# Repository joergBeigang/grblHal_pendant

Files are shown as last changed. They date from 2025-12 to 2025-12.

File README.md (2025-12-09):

# grblHal_pendant
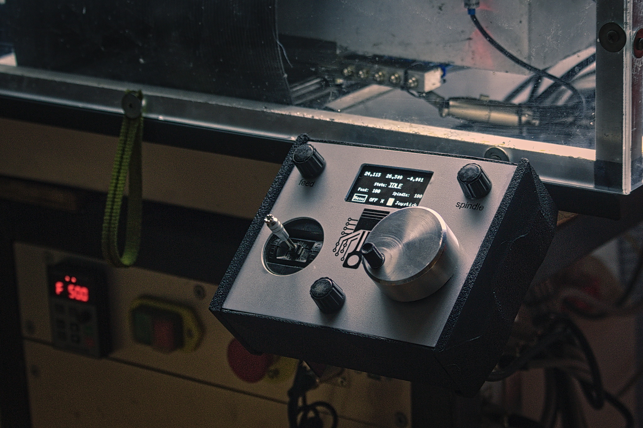
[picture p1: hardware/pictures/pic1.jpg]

This is a simple pendant for [grblHal](https://github.com/grblHAL/core) controlled cnc machines. It is running on an ESP32. For the analog feel it is using a high resolution rotary encoder (with 600 pulses per revolution), and an analog joystick for rapid movement.

There are in total 3 EC11 rotary encoders with button functionality. Two to dial in the feed and spindle overrides, and one for navigating the menu. The display is a I2C OLED (SSD1309) with 128x64 pixel resolution.

I chose those components mostly because I already had them laying around — the rotary encoder came out of an old pendant I made for 8bit grbl back then, the joystick out of an old RC controller. EC11s and the OLED display can be ordered very cheaply from China.

I am aware that my choice for the encoder for jogging is a little bit unconventional, and therefore building a pendant like this is not for everyone, but at least some code snippets might be useful for others.

All the jogging, regardless if joystick or encoder, is done by reading the input device at a frequency of 10Hz. I figured that is a good frequency to feed jogging commands to grbl or grblHal. The revolution of the rotary encoder is translated directly into the revolution of my ball screw, so one revolution moves the machine by 5mm. 1200 edges per revolution means that one pulse equals 0.0042mm movement. With the given time interval of 0.1 seconds the feed is easy to calculate and it has the nice side effect that there is no need for any stop-jog real-time commands. This gives a pretty secure feeling when jogging.

I personally often like to touch off with a running spindle, when preparing stock with an indexed end mill for example. And like this, this feels really smooth.

The UART mode of grblHal is enabled and disabled automatically. So you can switch between the computer and pendant without pressing any buttons. GrblHal needs to be configured with UART mode enabled and rt command for switching over.

---

## Building

The code uses the Arduino framework and a few libraries:

- **U8g2lib.h** and **Wire.h** – for the display  
- **Button.h** and **AiEsp32RotaryEncoder.h** – for the buttons of the EC11 encoders  
- **Preferences.h** – for saving settings in the ESP32  
- **queue** – for streaming gcode  
- **math.h**

It can be compiled and uploaded with the Arduino IDE or the Arduino CLI tools.

Pin assignments and the definition of the pulses per revolution of the rotary encoder can be found in `config.h`. The analog joystick needs to be calibrated first; this can be done in the menu of the pendant. This is important — otherwise the machine might move unexpectedly as soon as joystick input is selected.

---

## Hardware

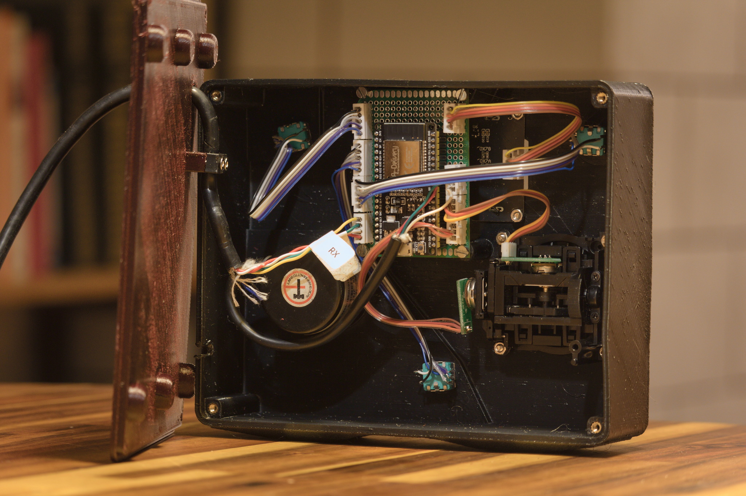
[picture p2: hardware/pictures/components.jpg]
components


In the hardware folder is a schematic and CAD files of the case. I am using 3mm alu dipond as front panel (again, because I found some in my garage). 3mm is a pretty unusual thickness for front panels, so most likely the model needs to be adapted a little, or just 3D-print a spacer that goes under the panel.

And yes, the case is quite big — that's because I'm not a big fan of handheld devices. I prefer it mounted to the CNC so I have one hand free to slide a parallel around on the work piece or similar.

List of components:

- 1 rotary encoder LPD3806-600BM-G5-24G
- 3 rotary encoders EC11
- 1 OLED display 128x64 pixel I2C with SSD1309 driver
- 1 analog joystick
- 1 ESP32 Development board
- 1 bidirectional 2 channel level shifter
- cables and connectors

---

## USE

All the pins, the pulses per revolution of the rotary encoder for jogging and the distance pro revolution are set in config.h.
When it's all connected, and the firmware is flashed the display should show up. 
It needs to be setup in Menu -> Settings:

- Joystick settings
  - Calibrate Joystick - calibration process for the analog joystick 
  - joystick invert X, Y - invert the axis
  - set joystick speed - it is not a real world unit. Standard is 3, 5 gives you about 4200 mm/min feed when jogging full speed in xy direction (diagonal), if Z is moved simultaneous, the feed is higher.

- Encoder settings - invert X, Z and Z
- delay compensation - compensates for delay (processing, acceleration). smaller value give a directer control, less overshoot, higher value smoother movement in higher speeds. Default is 0, values like 0.1 to 0.25 can smoothen joystick jogging

- **Button.h** and **AiEsp32RotaryEncoder.h** – for the buttons of the EC11 encoders  

---

## Disclaimer

Use at your own risk: read the source code first. Don't crash the machine or even hurt yourself.

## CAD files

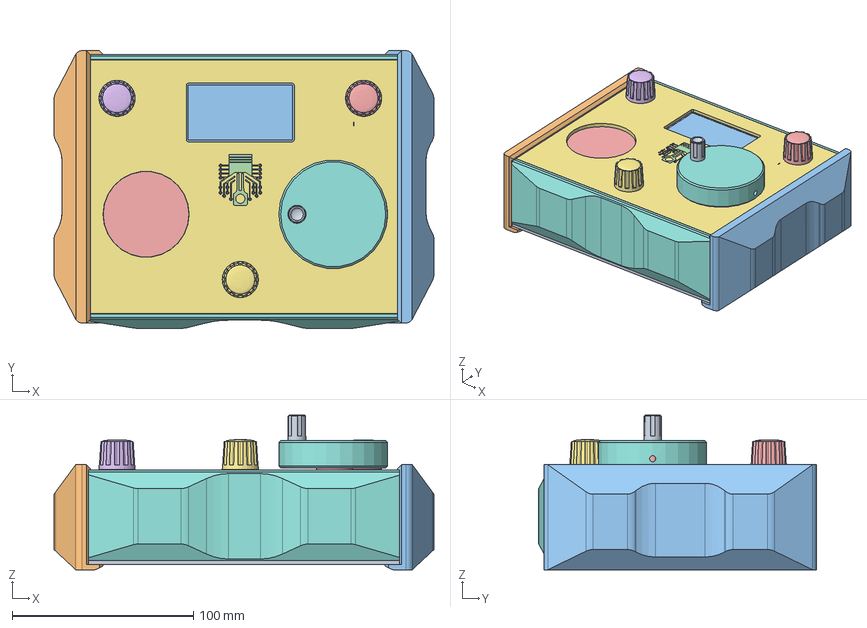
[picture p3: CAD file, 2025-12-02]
hardware/grblHal_pendant_case.FCStd
209.6 x 153.2 x 85.3 mm
ShapeString
ShapeString001
ShapeString002
knob
knob002
knob001
encoder_disk
cable_block
OLED
XH-4P
Joystick
ESP32
a
b
c
d
e
f
rotary_encoder
board
front_panel
case_upper
case_lower
side_cover
side_cover (mirrored)

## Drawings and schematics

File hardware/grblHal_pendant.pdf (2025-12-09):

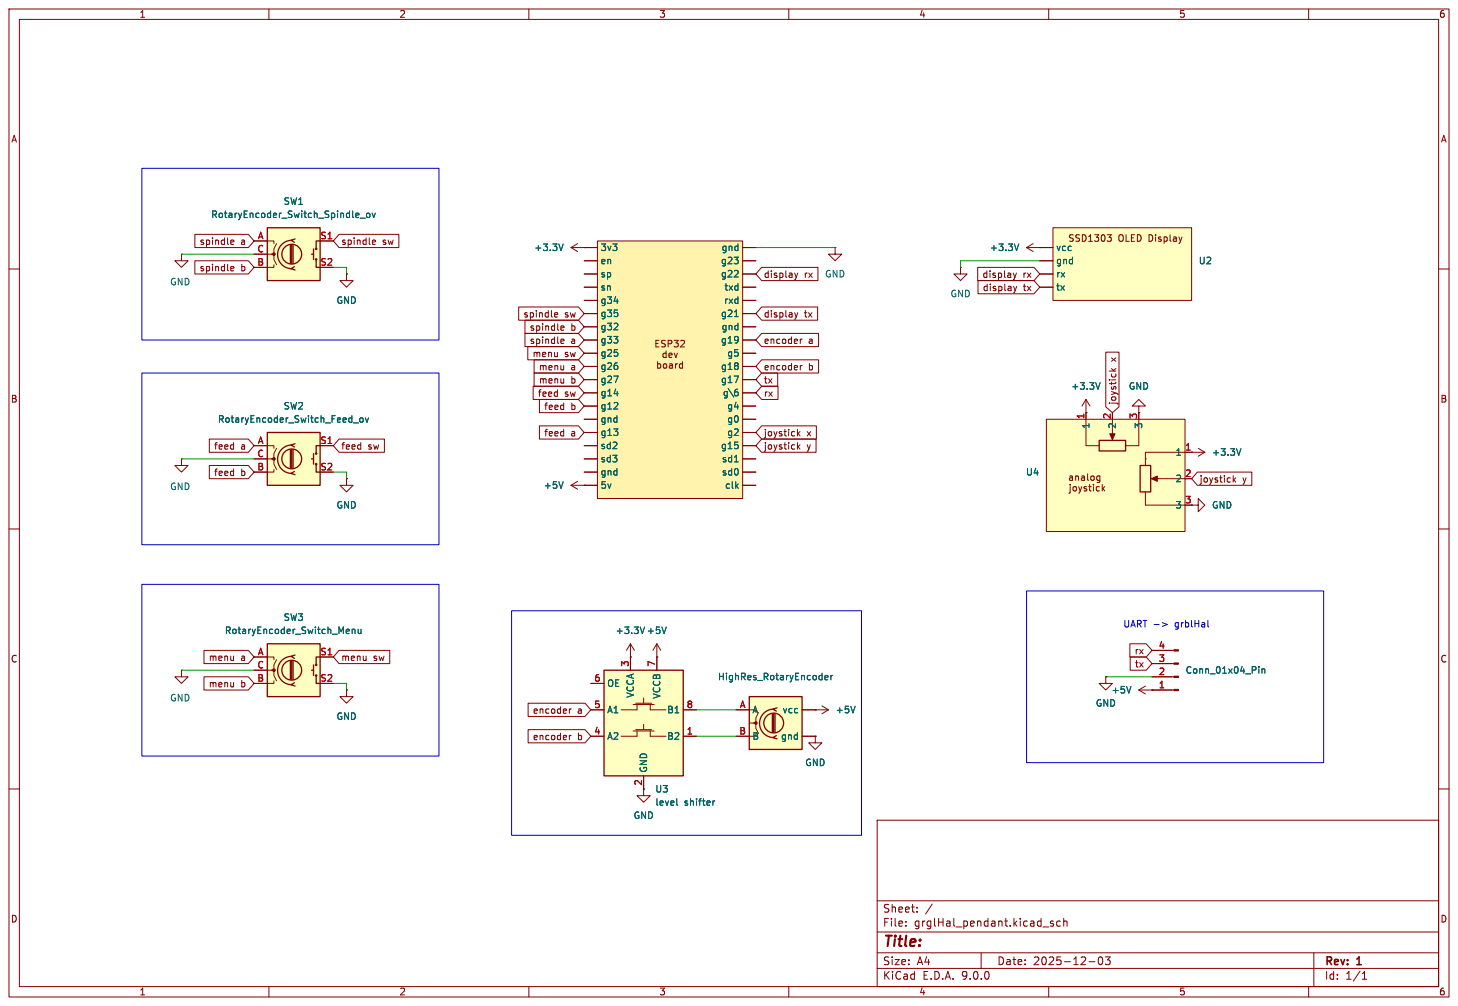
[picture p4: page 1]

Id: 1/1 Title: File: grglHal_pendant.kicad_sch Sheet: /

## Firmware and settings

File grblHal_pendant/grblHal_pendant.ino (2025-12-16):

/*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
grblMachinist is distributed in the hope that it will be useful,
but WITHOUT ANY WARRANTY;
without even the implied warranty of MERCHANTABILITY or FITNESS FOR A PARTICULAR
PURPOSE.
See the GNU General Public License for more details.

You should have received a copy of the GNU General Public License along with
grblMachinist.
If not, see <https://www.gnu.org/licenses/>.
*/

#include <U8g2lib.h>
#include <Wire.h>
#include <math.h>
#include <Button.h>
#include "AiEsp32RotaryEncoder.h"
#include "config.h"
#include "settings.h"
#include "encoder.h"
#include "joystick.h"
#include "parser.h"
#include "gui_render.h"
#include "gui_build.h"
#include "gui_menu_actions.h"
#include <Preferences.h>
#include "ec11_encoder.h"
#include "stream.h"

Preferences prefs;
// instace the settings struct
Settings settings;

// selected menu item
int selectedIndex = -1;          // 1 = off is selected on startup

// to keep UART active while
volatile bool keepActive = false; 

// timer for real time command, used for swtiching on in 
// joystick and encoder reading to avoid too fast switching
// and grblHal freezinguG
long rtCmdTimer = 0;

// timer for swtiching off UART Mode. 
// needs to be reset to keep UART active
// used for jogging with encoder and joyustick
long timerEncoderRest  = 0;

// position of the cursor in the menu
int cursorPosition = 0; 

// mode = operation mode
// 0 - off
// 1 - joystick mode
// 2 - X axis encoder mode
// 3 - Y axis encoder mode
// 5 - machine is in run state
int mode = 0;                   

// the value that is edited in the menu via menu encoder
float valueEdit = 0.0;  

// pointer to valueEdit to use in struct (expects pointer)
float  *pValueEdit = &valueEdit;


// instace of struct that collects all info send by grbl
GrblStatus grblStatus;

// display
U8G2_SSD1309_128X64_NONAME2_F_HW_I2C u8g2(U8G2_R0, U8X8_PIN_NONE);

// E11 rotary encoders
// rotary encoder menu
AiEsp32RotaryEncoder rotaryMenu(MENU_A, MENU_B, -1, -1, 4);
// rotary encoder feed override
AiEsp32RotaryEncoder rotarySpindle(SPINDLE_A, SPINDLE_B, -1, -1, 4);
// rotary encoder spindle override
AiEsp32RotaryEncoder rotaryFeed(FEED_A, FEED_B, -1, -1, 4);

// buttons of rotary encoders, button libraray for easier release detection
Button buttonMenu(MENU_SW);
Button buttonFeed(FEED_SW);
Button buttonSpindle(SPINDLE_SW);

// ISR – reading the EC11 encoders
void IRAM_ATTR readEncoderISR() {
  rotaryMenu.readEncoder_ISR();
  rotaryFeed.readEncoder_ISR();
  rotarySpindle.readEncoder_ISR();
}


// give grblStatus some initial values not avoid pointer errors
void initGrblStatus(){
  grblStatus.status = "NONE";
  grblStatus.position[0] = -331.0;
  grblStatus.position[1] = -912.0;
  grblStatus.position[2] = -183.0;
  grblStatus.overRides[0] = 100.0;
  grblStatus.overRides[1] = 100.0;
  grblStatus.overRides[2] = 100.0;
  grblStatus.coordinateSystem = 54;
}


void setup() {
  // initial values of grblStatus
  initGrblStatus();
  // peferences
  prefs.begin("settings");
  readSettings();
  // Serial
  // Serial usb for debugging
  Serial.begin(115200);
  // Serial uart for grblHAL communication
  Serial2.begin(115200, SERIAL_8N1, GRBL_RX, GRBL_TX);
  // wire for display
  Wire.begin(21, 22);
  u8g2.begin();
  // analog read for joystick
  analogReadResolution(12);
  // Rotary encoder for Jogging
  // pullups
  pinMode(ENCODER_A, INPUT_PULLUP);
  pinMode(ENCODER_B, INPUT_PULLUP);
  pinMode(MENU_A, INPUT_PULLUP);
  pinMode(MENU_B, INPUT_PULLUP);
  pinMode(FEED_A, INPUT_PULLUP);
  pinMode(FEED_B, INPUT_PULLUP);
  pinMode(SPINDLE_A, INPUT_PULLUP);
  pinMode(SPINDLE_B, INPUT_PULLUP);
  initRotaryEncoders();

  // variables for reading the high resolution encoder
  lastA = digitalRead(ENCODER_A);
  lastB = digitalRead(ENCODER_B);

  // interrupts for encoder reading
  attachInterrupt(digitalPinToInterrupt(ENCODER_A), encoderISR, CHANGE);
  attachInterrupt(digitalPinToInterrupt(ENCODER_B), encoderISR, CHANGE);
  drawScreen(0);

  // check if there are valid joystick settings set, if not start 
  // the calibration process
  checkJoystickSettings();
}

// send real time command 0x8B to enable/disable uart command
void toggleEnable(){
  uint8_t byteToSend = 0x8B;
  Serial2.write(byteToSend);
  rtCmdTimer = millis();
  DEBUG_PRINTLN("ENABLE/DISABLE");
  DEBUG_PRINTLN(grblStatus.uartMode);

  if (grblStatus.uartMode == true) {
    timerEncoderRest = millis();
  }
}

// disable UART mode after a defined period without any user 
// input via joustick or rotatary encoder
void disableTimer(){
  if (keepActive == true) {
    timerEncoderRest = millis();
  };
  long currentMillis = millis();

  if (currentMillis - timerEncoderRest >= CANCEL_UART_TIMER) {
  // switch off uart mode
      if (grblStatus.uartMode == 1){
        resetQueue();
        toggleEnable();
        DEBUG_PRINTLN("UAERT off");
      }
  }
}

// triggered every .1 seconds
void modeLogic(){
 switch (mode){
   case 0:
     if (currentPage == &rootPage) selectedIndex = 1;
     break;
   case 1:
     readJoystick();
     break;
   case 2:
     readJogEncoder(String("X"));
     break;
  case 3:
     readJogEncoder(String("Y"));
     break;
  case 5:
    currentPage = &runPage;
    cursorPosition = 0;
     break;
 }
}


// setting the mode based on the machine status
// run everytime the parser found a grbl status report
void setMode(){
  static int previousMode = mode;
  int chk1 = grblStatus.status.indexOf("RUN"); 
  int chk2 = grblStatus.status.indexOf("HOLD"); 
  if (chk1 != -1 || chk2 != -1) {
    mode = 5;
    previousMode = 5;
    currentPage = &runPage;
    selectedIndex = 1;  // pause button is highlighted
    return;
  } else {
    if (previousMode == 5){
      currentPage = &rootPage;
      // machine just stopped running, go back to previous mode
      mode = 0;
      selectedIndex = 1; // off is highlighted
      previousMode = 0;
      return;
    }
  }

}


// read UART from grblHAL
void readUart(){
  static String grblInfo;
  while (Serial2.available()) {
    char c = Serial2.read();
    grblInfo += c;

    if (c == '\n') {
        setMode();
        bool chk = parseGrblOutput(grblInfo);
        grblInfo = "";    // reset after full line is received
    }
  }
}

void loop() {
  // timer for disabling uart mode automatically after 1 sec of not using it
  disableTimer();
  // read the rotary encoders for menu
  rotaryMenuLoop();
  // switches of all ec11 rotary encoders
  overRideSwitches();
  // read grblHals ouput
  readUart();
  // stream gcode to grblHal
  processQueue();

  static unsigned long timerJog = 0;  // will store last time encoder was read
  unsigned long currentMillis = millis();
  if (currentMillis - timerJog >= 100) {
    // set the right mode based on grblhal's status
    modeLogic();
    // update feed and spindle overrides 
    rotaryFeedLoop();
    rotarySpindleLoop();
    // redreaw the screen
    drawScreen(cursorPosition);
    // reset the timer
    timerJog = currentMillis;
  }
}

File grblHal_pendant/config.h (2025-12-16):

/*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
grblMachinist is distributed in the hope that it will be useful,
but WITHOUT ANY WARRANTY;
without even the implied warranty of MERCHANTABILITY or FITNESS FOR A PARTICULAR
PURPOSE.
See the GNU General Public License for more details.

You should have received a copy of the GNU General Public License along with
grblMachinist.
If not, see <https://www.gnu.org/licenses/>.
*/
// set to 0 to disable all debug printing on Serial (usb)
#define DEBUG 1

// pins for uart communicatino with grblhal
#define GRBL_RX 16
#define GRBL_TX 17

// mm travel for each full ratation of the jog encoder
#define MM_PER_REVOLUTION 5
// pulses per revolution of the jog encoder
#define PULSES_PER_REVOLUTION 600
// interval for sending jog commands in ms
#define SEND_INTERVAL 100


// Jogging joyustick
#define JOY_X_PIN 2  // GP26, ADC0
#define JOY_Y_PIN 15

#define JOY_MAX_FEED 3000

// ************************
// rotray encoder pin setup
// ************************
//
// Jogging rotary encoder
// encoder for jogging
#define ENCODER_A 18
#define ENCODER_B 19

// EC11 rotary encder
// menu
#define MENU_A 26
#define MENU_B 27
#define MENU_SW 25

// feed overrides
#define FEED_A 13
#define FEED_B 12
#define FEED_SW 14

// spindle overrides
#define SPINDLE_A 33
#define SPINDLE_B 32
#define SPINDLE_SW 4

// *********************
// rotary encoder invert
// *********************
// 1 = invert is true
// 0 = invert is false
#define MENU_INVERT 1


// timer for swtiching back from UART mode to normal mode 
// after last input via joystick or encoder
// time in milli seconds
#define CANCEL_UART_TIMER 600

#if DEBUG
  #define DEBUG_PRINT(x)     Serial.print(x)
  #define DEBUG_PRINTLN(x)   Serial.println(x)
#else
  #define DEBUG_PRINT(x)
  #define DEBUG_PRINTLN(x)
#endif

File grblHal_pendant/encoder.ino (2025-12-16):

/*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
grblMachinist is distributed in the hope that it will be useful,
but WITHOUT ANY WARRANTY;
without even the implied warranty of MERCHANTABILITY or FITNESS FOR A PARTICULAR
PURPOSE.
See the GNU General Public License for more details.

You should have received a copy of the GNU General Public License along with
grblMachinist.
If not, see <https://www.gnu.org/licenses/>.
*/
/*
 * functions for reading rotary encoders
 */

volatile int32_t encoderPos = 0;
String jogAxis = "x";
long lastPos = 0;           // Changed to non-static for access from main.ino

const long interval = float(SEND_INTERVAL);         // interval for sending jog commands in milliseconds

long timerEncoder = 0;


// interrupt based encoder reading
void encoderISR() {   // just remove IRAM_ATTR
  bool a = digitalRead(ENCODER_A);
  bool b = digitalRead(ENCODER_B);

  if (a != lastA) {
    encoderPos += (a == b) ? 1 : -1;
  }
  lastA = a;
  lastB = b;
}


// initialize the encoder to avoid unwanted movment when activating
void initEncoder() {
  DEBUG_PRINTLN("init encoder");
  lastPos = encoderPos;
}


// run every .1 sec
void readJogEncoder(String axis){
  static int32_t lastPos = 0;
  // Set active if encoder moved (based on encoderPos change)
  float mm = readEncoderPos();
  if (mm != 0) {
    // check for invert
    if (invertAxis(axis) == true) mm = -mm;
    DEBUG_PRINTLN("encoder moved");
    // deal with uart mode and respect the minimum time span 
    // between sending real time commands
    timerEncoderRest = millis();
    if (grblStatus.uartMode == 0){
      DEBUG_PRINTLN("UART active");
      if (millis() - rtCmdTimer < 200) return;
      toggleEnable();
    }
    // build jog command
    String cmd = calculateCmd(mm, axis);
    // send jog command
    sendToGrbl(cmd);
  }
}


// check the settings if the axis should be inverted
bool invertAxis(String axis) {
  if (axis == "X" && settings.encoderInvertX == true) return true;
  if (axis == "Y" && settings.encoderInvertY == true) return true;
  if (axis == "Z" && settings.encoderInvertZ == true) return true;
  return false;
}


// read the encoder and return the distance moved in mm
float readEncoderPos(){

  if (lastPos!= encoderPos) {
    int difPos= encoderPos - lastPos;
    lastPos = encoderPos;
    float mm = calculateEncoderDistance(difPos);
    return mm;
  }
  return 0.0;
}


// translate the encoder steps into mm distance
float calculateEncoderDistance(int steps){
    // one revolution is 10mm
    // 1200 steps per revolution
    float neg = 1.0;
    if (steps < 0){
      neg = -1.0;
      steps = abs(steps);
    }
    return ((float(steps) / 1200.0) * 5.0) * neg;
}


// builds the command with correct feedrate
String calculateCmd(float mm, String axis){
  // float feed = abs(mm * (60000 / float(interval)))*1.2;
  float feed = abs(mm * (60000 / float(interval)));
  String cmd = "$J=G91 ";
  cmd += axis;
  cmd += String(mm, 3);
  cmd += " F";
  cmd += feed;
  cmd += "\n";
  return cmd;
}

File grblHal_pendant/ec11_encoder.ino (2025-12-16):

/*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
grblMachinist is distributed in the hope that it will be useful,
but WITHOUT ANY WARRANTY;
without even the implied warranty of MERCHANTABILITY or FITNESS FOR A PARTICULAR
PURPOSE.
See the GNU General Public License for more details.

You should have received a copy of the GNU General Public License along with
grblMachinist.
If not, see <https://www.gnu.org/licenses/>.
*/

/*
 * all functions for the ec11 encoder 
 * for feed and spindle override 
 * and menu
 */

int lastValue = 0;
bool setValueMode = false;
int rotatryMenuLastPos = 0;
float valueEditIncrement = .1;
float valueEditMin = -9999;
float valueEditMax = 9999;

// instace stuct with rt commands for overrides
Overrides feedOv = {0, 0x93, 0x91, 0x94, 0x92};
Overrides spindleOv = {0, 0x9C, 0x9A, 0x9D, 0x9B};


// Setup EC11 Rotary Encoders
void initRotaryEncoders() {
  rotaryMenu.begin();
  rotaryMenu.setup(readEncoderISR);
  rotaryMenu.disableAcceleration();

  rotaryFeed.begin();
  rotaryFeed.setup(readEncoderISR);
  rotaryFeed.disableAcceleration();

  rotarySpindle.begin();
  rotarySpindle.setup(readEncoderISR);
  rotarySpindle.disableAcceleration();
  // buttons 
  buttonMenu.begin();
  buttonFeed.begin();
  buttonSpindle.begin();
}


// *********
// overrides
// *********

void sendOverrideCommands(Overrides &ov){
  if (ov.difference > 10) {
    Serial2.write(ov.cmdTen);
    ov.difference -= 10;
  } else if (ov.difference > 0) {
    Serial2.write(ov.cmdOne);
    ov.difference -= 1;
  }
  if (ov.difference < -10) {
    Serial2.write(ov.cmdTenMinus);
    ov.difference += 10;
  } else if (ov.difference < 0) {
    Serial2.write(ov.cmdOneMinus);
    ov.difference += 1;
  }
}

// setting feed or spindle override via button release back to 100
void overRideSwitches(){
	if (buttonFeed.released()) {
    DEBUG_PRINTLN("feed 100");
    uint8_t byteToSend = 0x90;
    Serial2.write(byteToSend); 
  }
	if (buttonSpindle.released()) {
    DEBUG_PRINTLN("spindle 100");
    uint8_t byteToSend = 0x99;
    Serial2.write(byteToSend); 
  }
}


void rotaryFeedLoop(){
  static int rotatryFeedLastPos = 0;
  if (rotaryFeed.encoderChanged()) {
    int movement = rotaryFeed.readEncoder();  // cumulative steps since last reset
    int dif = movement - rotatryFeedLastPos;
    rotatryFeedLastPos = movement;
    feedOv.difference += dif;
  }
  sendOverrideCommands(feedOv);
}

void rotarySpindleLoop(){
  static int rotatrySpindleLastPos = 0;
  if (rotarySpindle.encoderChanged()) {
    int movement = rotarySpindle.readEncoder();  // cumulative steps since last reset
    int dif = movement - rotatrySpindleLastPos;
    rotatrySpindleLastPos= movement;
    spindleOv.difference += dif;
  }
  sendOverrideCommands(spindleOv);
}


// **************
// menu functions
// **************

void setValue(){
  int inverter = 1;
  if (MENU_INVERT == 1){
    inverter = -1;
  }
    int movement = rotaryMenu.readEncoder();  // cumulative steps since last reset
                                              // S
    valueEdit = float((movement * valueEditIncrement)*inverter);
    if (valueEdit < valueEditMin) valueEdit = valueEditMin;
    if (valueEdit > valueEditMax) valueEdit = valueEditMax;
}

void moveCursor(){
  int inverter = 1;
  if (MENU_INVERT == 1){
    inverter = -1;
  }
    int movement = rotaryMenu.readEncoder();  // cumulative steps since last reset
    int dif =(movement-rotatryMenuLastPos) * inverter;
    cursorPosition += dif;
    if (cursorPosition < 0) cursorPosition = 0;
    if (cursorPosition >= currentPage -> menuCount) cursorPosition = currentPage -> menuCount - 1;
      rotatryMenuLastPos = movement;
}

void rotaryMenuLoop(){
  if (rotaryMenu.encoderChanged()) {
    if (setValueMode == false) moveCursor();
    if (setValueMode == true) setValue();
    drawScreen(cursorPosition);
    }
	
	if (buttonMenu.released()) {
    // drawScreen(cursorPosition);
    // MenuItem &item = rootMenu[cursorPosition];
    MenuItem &item = currentPage->menuItems[cursorPosition];

    if (item.action != nullptr){
      item.action();
    }
  }
}

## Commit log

2025-12-01 rc 01
    [config.h]
2025-12-01 Add initial README for grblHal pendant project
2025-12-02 Fix movement precision in README
    Corrected the precision of movement calculation from 0.004166mm to 0.0042mm.
2025-12-02 calibration bug fixed
    [grblHal_pendant_case.FCStd]
2025-12-02 calibration spike removel and sanity check
2025-12-03 calibration: just median, not spike removal
2025-12-03 variable renamed, ui fix
    [config.h]
2025-12-04 gui set value fixed
    [ec11_encoder.ino, encoder.ino, gui_build.ino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]
2025-12-04 shortest move to .001
    [encoder.ino]
2025-12-05 Update README with grblHal link
2025-12-05 Fix typo in jogging input device description
    Corrected the description of rotary encoder pulses per revolution.
2025-12-05 Fix typo in README for rotary encoders
2025-12-08 added CANCEL_UART_TIMER
    [config.h]
2025-12-15 string bug in build command fixed (now 1/1000 mm resolution)
    [encoder.ino]
2025-12-15 menu for inverting encoder fixed
    [gui_build.ino, gui_menu_actions.ino]
2025-12-15 added invert for z axis (enocer)
    [joystick.ino]
2025-12-16 licese info added
    [config.h]

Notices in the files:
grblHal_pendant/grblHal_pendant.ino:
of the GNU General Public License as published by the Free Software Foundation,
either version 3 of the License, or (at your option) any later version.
